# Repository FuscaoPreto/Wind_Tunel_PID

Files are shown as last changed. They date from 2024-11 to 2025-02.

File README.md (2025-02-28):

# Wind Tunnel Speed Control using PID

This project involves controlling the speed of a wind tunnel fan using a PID controller. The system uses environmental data from multiple sensors to compute airspeed and adjusts the fan speed accordingly.

The PID gains were discoveres by applying the Ziegler-Nichols method as a ruler.

## Sensors and Measurements

The project utilizes the following sensors:
- **HDC1080**: Measures temperature and humidity.
- **BME280**: Measures barometric pressure.
- **MPXV7002DP**: Measures differential air pressure.

## Airspeed and Air Density Calculation

The airspeed is derived using the Pitot tube formula, which relates the air pressure difference to velocity. The air density is computed using environmental measurements:

1. **Temperature in Kelvin**:
   $$T_k = T_{\text{Celsius}} + 273.15$$

2. **Saturation vapor pressure**:
   $$P_{\text{sat}} = 0.61078 \cdot \exp\left(\frac{17.27 \cdot T_{\text{Celsius}}}{T_{\text{Celsius}} + 237.3}\right)$$

3. **Water vapor pressure**:
   $$P_v = P_{\text{sat}} \cdot \frac{\text{Humidity}}{100.0}$$

4. **Dry air pressure**:
   $$P_d = P_{\text{atmospheric}} - P_v$$

5. **Air density**:
   $$\rho = \frac{P_d}{287.058 \cdot T_k} + \frac{P_v}{461.495 \cdot T_k}$$

6. **Airspeed**:
   $$v = \sqrt{\frac{2 \cdot P_{\text{differential}}}{\rho}}$$

## PID Control

The system employs a PID controller to maintain the target airspeed by adjusting the fan's speed.

### PID Formula
$$\text{PID output} = K_p \cdot e + K_i \int e \, dt + K_d \frac{de}{dt}$$

- **Proportional (P)**: $`e = v_{\text{target}} - v_{\text{measured'}}`$
- **Integral (I)**: Accumulated error over time.
- **Derivative (D)**: Rate of change of error.
#### Note:
The error in the code itself is multiplied by a air speed to RPM constant which is unique to my project, this is needed to calculate the correct PWM duty cycle.

## Code Logic

### Initialization
- Configure sensors (HDC1080 and BME280) using I²C.
- Initialize moving average arrays for pressure and RPM readings.
- Set up PWM for fan speed control.
- Attach an interrupt for tachometer readings.

### Main Functions
#### `updateData()`
Reads data from sensors and calculates:
- Air density ($`\rho`$)
- Airspeed ($`v`$)

#### `tacometroInterrupt()`
Triggered on tachometer pulses:
- Calculates RPM.
- Updates moving averages for RPM and pressure.
- Computes airspeed and PID output.
- Adjusts fan speed via PWM.

#### `loop()`
Continuously prints real-time data for debugging.

### Hardware Configuration
- **Analog Pin (1)**: Reads differential pressure sensor.
- **Tachometer Pin (15)**: Measures fan RPM.
- **PWM Pin (16)**: Controls fan speed.
- **SDA Pin (12), SCL Pin (11)**: I²C communication with HDC1080 and BME280.

## Libraries Used
- [ClosedCube_HDC1080](https://github.com/closedcube/ClosedCube_HDC1080)
- [BME280](https://github.com/finitespace/BME280)

## Setup and Usage
1. Connect the sensors and configure pins as per the hardware setup.
2. Upload the code to an Arduino or ESP32 board.
3. Adjust PID constants (`K_p`, `K_i`, `K_d`) for your wind tunnel.
4. Monitor serial output for real-time airspeed and PID performance.

## Images

Here are photos of the wind tunnel setup and key components:
   Body:
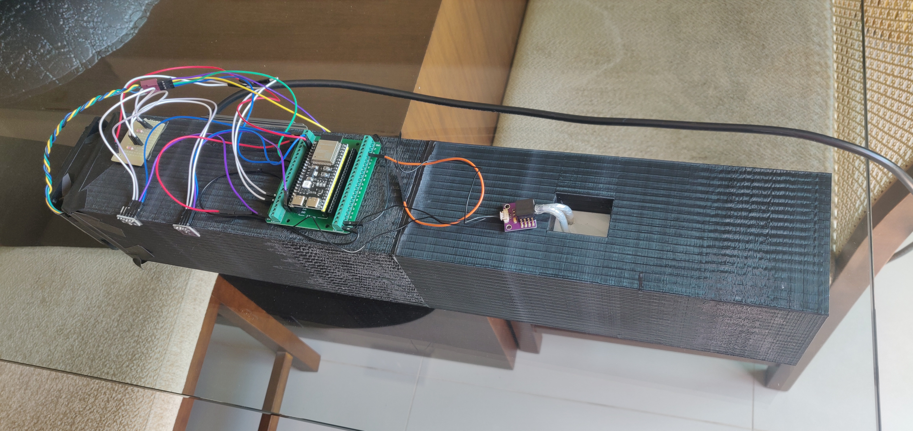
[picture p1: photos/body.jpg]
body
      
   Body (Alternate View):
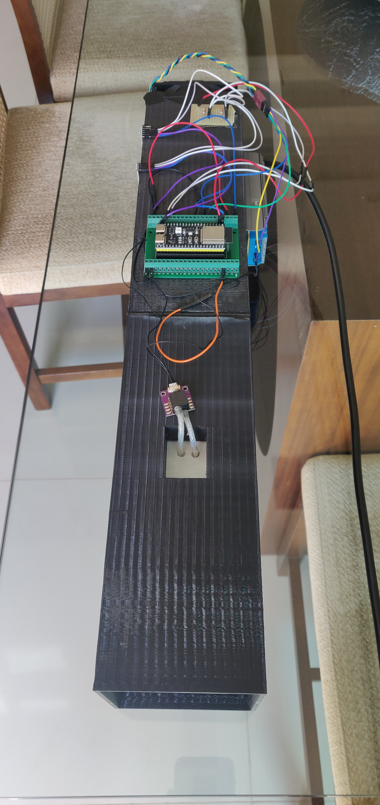
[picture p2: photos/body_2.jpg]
body vertical
      
   Mouth (Pitot Tube View):
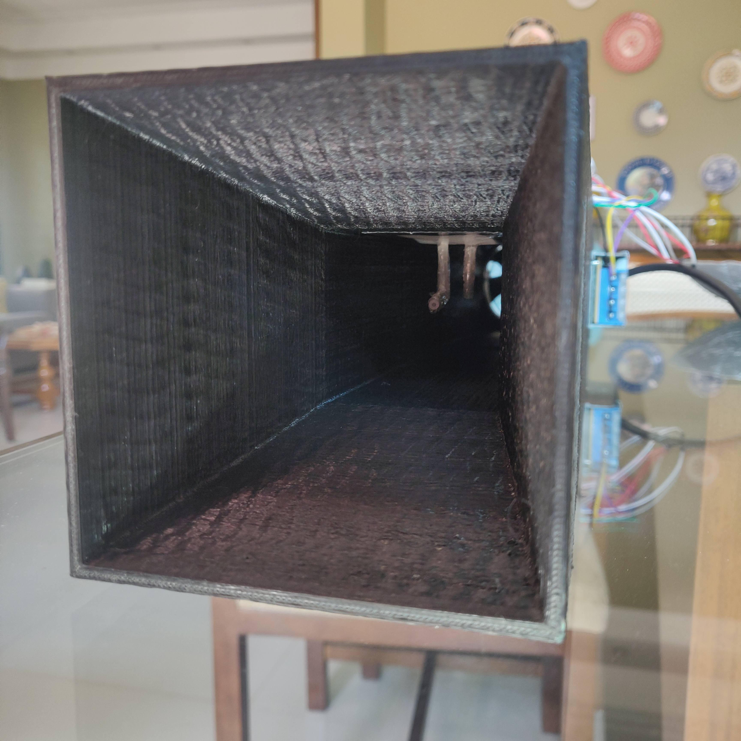
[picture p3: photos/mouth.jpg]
mouth


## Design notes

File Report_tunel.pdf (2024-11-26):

# Report tunel

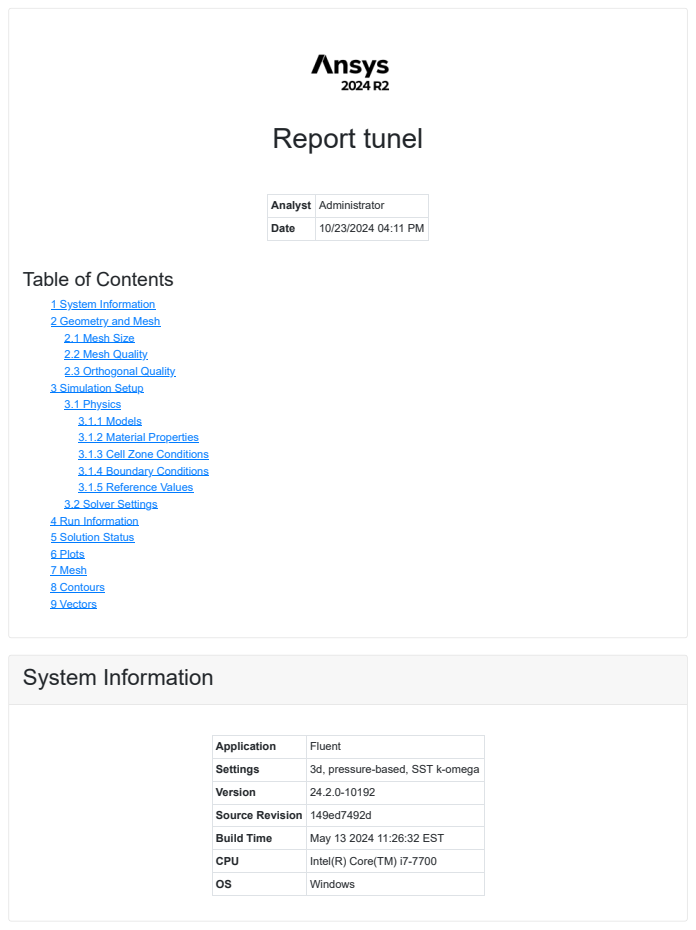
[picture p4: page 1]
System Information

Analyst | Administrator
Date | 10/23/2024 04:11 PM

Table of Contents

1 System Information
2 Geometry and Mesh
2.1 Mesh Size
2.2 Mesh Quality
2.3 Orthogonal Quality
3 Simulation Setup
3.1 Physics
3.1.1 Models
3.1.2 Material Properties
3.1.3 Cell Zone Conditions
3.1.4 Boundary Conditions
3.1.5 Reference Values
3.2 Solver Settings
4 Run Information
5 Solution Status
6 Plots
7 Mesh
8 Contours
9 Vectors

Application | Fluent
Settings | 3d, pressure-based, SST k-omega
Version | 24.2.0-10192
Source Revision | 149ed7492d
Build Time | May 13 2024 11:26:32 EST
CPU | Intel(R) Core(TM) i7-7700
OS | Windows

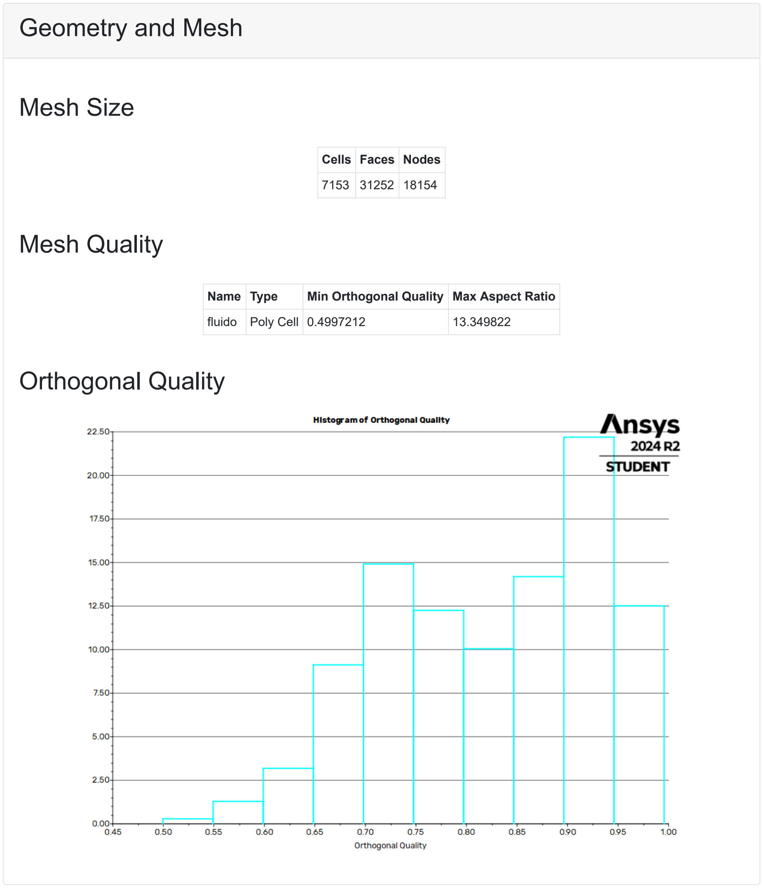
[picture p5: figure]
Geometry and Mesh; Mesh Size; Mesh Quality; Orthogonal Quality; Cells; Faces; Nodes; Name; Type; Min Orthogonal Quality; Max Aspect Ratio; fluido; Poly Cell

# Simulation Setup

# Physics

# Models

# Material Properties

# Cell Zone Conditions

# Boundary Conditions

Model | Settings
Space | 3D
Time | Steady
Viscous | SST k-omega turbulence model

Fluid

- air
Density | 1.225 kg/m^3
Cp (Specific Heat) | 1006.43 J/(kg K)
Thermal Conductivity | 0.0242 W/(m K)
Viscosity | 1.7894e-05 kg/(m s)
Molecular Weight | 28.966 kg/kmol
- Solid

aluminum

Density | 2719 kg/m^3
Cp (Specific Heat) | 871 J/(kg K)
Thermal Conductivity | 202.4 W/(m K)
- Fluid

fluido

Material Name | air
Specify source terms? | no
Frame Motion? | no
Laminar zone? | no
Porous zone? | no
- Inlet
- failed-inlet-fluido
Reference Frame | Absolute
Gauge Total Pressure [Pa] | 0
Supersonic/Initial Gauge Pressure [Pa] | 0
Direction Specification Method | Normal to Boundary

# Solver Settings

# Reference Values

Build artificial walls to prevent reverse flow? | no
Turbulence Specification Method | Intensity and Viscosity Ratio
Turbulent Intensity [%] | 5
Turbulent Viscosity Ratio | 10
- Outlet

failed-outlet-fluido

Reference Frame | Relative to Adjacent Cell Zone
Mass Flow Specification Method | Mass Flow Rate
Mass Flow Rate [kg/s] | 0.1041667
Supersonic/Initial Gauge Pressure [Pa] | 0
Turbulence Specification Method | Intensity and Viscosity Ratio
Turbulent Intensity [%] | 5
Turbulent Viscosity Ratio | 10

Wall

- failed
Wall Motion | Stationary Wall
Shear Boundary Condition | No Slip
Wall Surface Roughness | Standard
Wall Roughness Height [m] | 0
Wall Roughness Constant | 0.5
Area | 1 m^2
Density | 1.225 kg/m^3
Enthalpy | 0 J/kg
Length | 1 m
Pressure | 0 Pa
Temperature | 288.16 K
Velocity | 1 m/s
Viscosity | 1.7894e-05 kg/(m s)
Ratio of Specific Heats | 1.4
Yplus for Heat Tran. Coef. | 300
Reference Zone | failed-outlet-fluido
- Equations
Flow | True
Turbulence | True
- Numerics
Absolute Velocity Formulation | True

Pseudo Time Explicit Relaxation Factors

Density | 1

Body Forces | 1
Turbulent Kinetic Energy | 0.75
Specific Dissipation Rate | 0.75
Turbulent Viscosity | 1
Explicit Momentum | 0.5
Explicit Pressure | 0.5
- Pressure-Velocity Coupling
Type | Coupled
Pseudo Time Method (Global Time Step) | True

Discretization Scheme

Pressure | Second Order
Momentum | Second Order Upwind
Turbulent Kinetic Energy | Second Order Upwind
Specific Dissipation Rate | Second Order Upwind
- Solution Limits
Minimum Absolute Pressure [Pa] | 1
Maximum Absolute Pressure [Pa] | 5e+10
Minimum Static Temperature [K] | 1
Maximum Static Temperature [K] | 5000
Minimum Turb. Kinetic Energy [m^2/s^2] | 1e-14
Minimum Spec. Dissipation Rate [s^-1] | 1e-20
Maximum Turb. Viscosity Ratio | 100000

# Run Information

Number of Machines | 1
Number of Cores | 1
Case Read | 2.746 seconds
Iteration | 243.856 seconds
AMG | 165.586 seconds
Virtual Current Memory | 0.49369 GB
Virtual Peak Memory | 1.49084 GB
Memory Per M Cell | 19.8388

# Solution Status

## Iterations: 1000

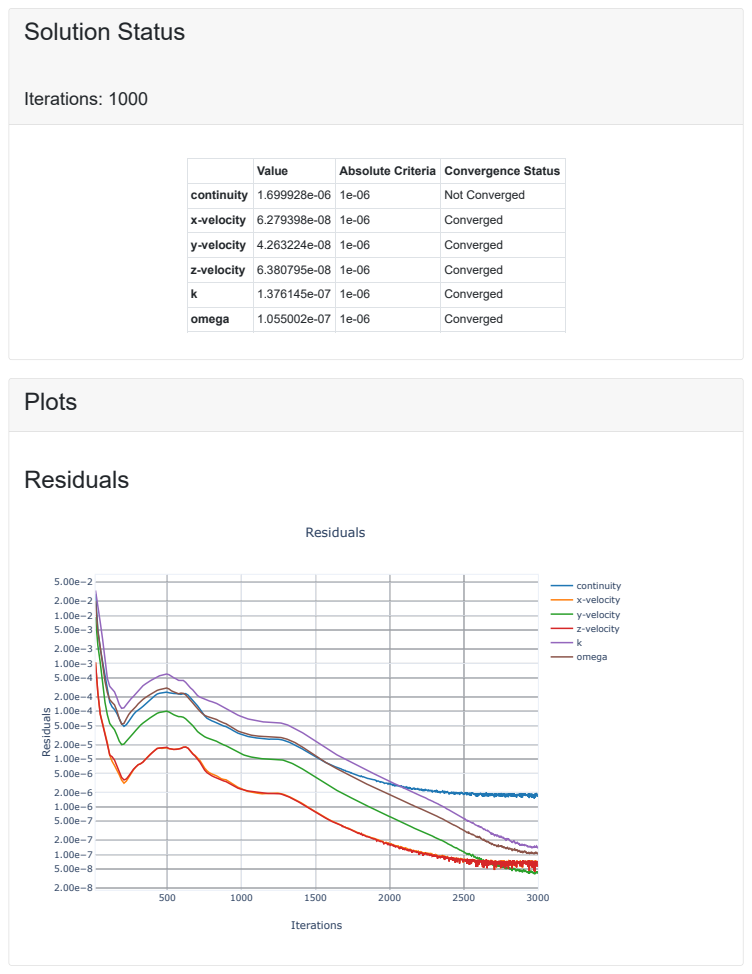
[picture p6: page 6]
Plots; Residuals; continuity; x-velocity y-velocity z-velocity k omega; Iterations

Value | Absolute Criteria | Convergence Status

continuity | 1.699928e-06 | 1e-06 | Not Converged
x-velocity | 6.279398e-08 | 1e-06 | Converged
y-velocity | 4.263224e-08 | 1e-06 | Converged
z-velocity | 6.380795e-08 | 1e-06 | Converged
k | 1.376145e-07 | 1e-06 | Converged
omega | 1.055002e-07 | 1e-06 | Converged

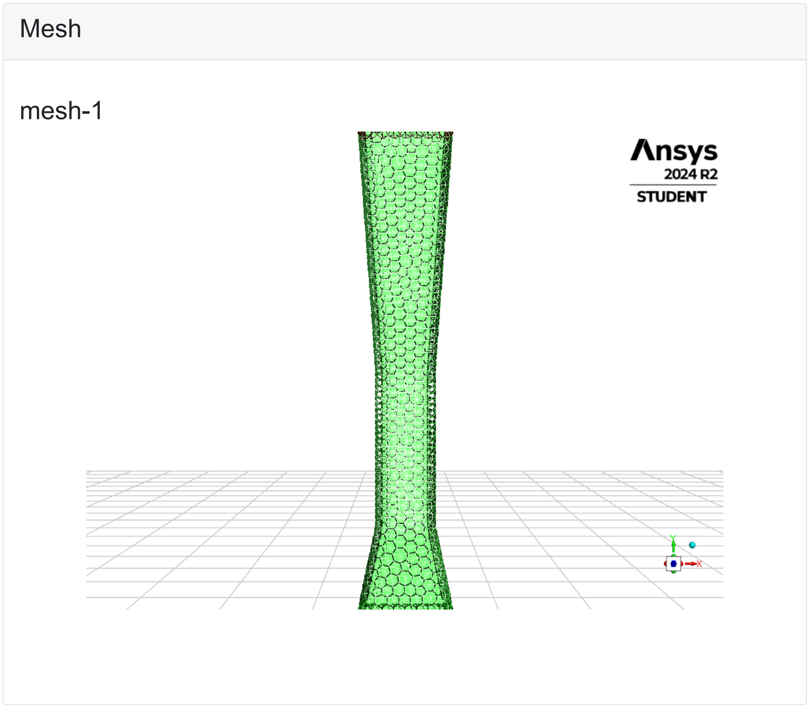
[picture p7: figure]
Mesh; mesh-1

# Contours

# turbulencia

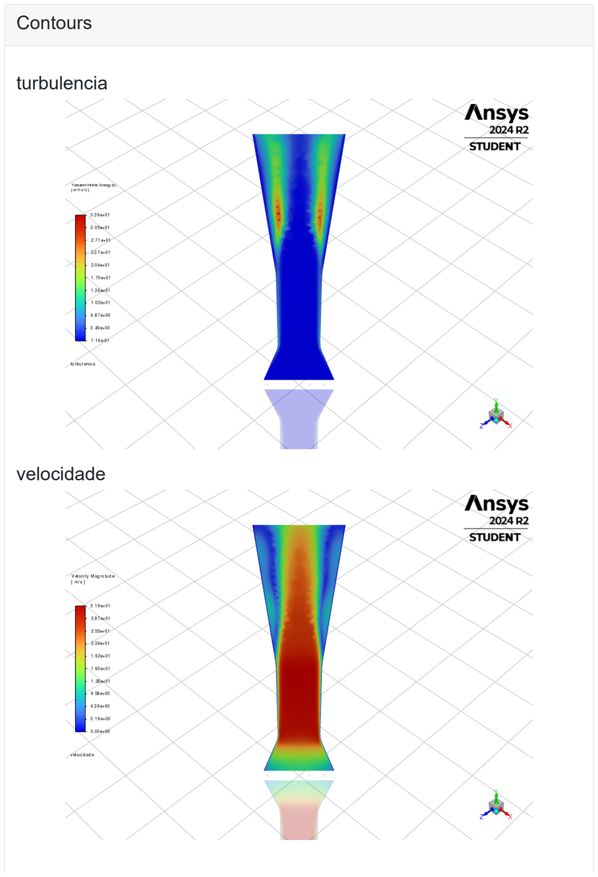
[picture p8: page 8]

# velocidade

# pressao

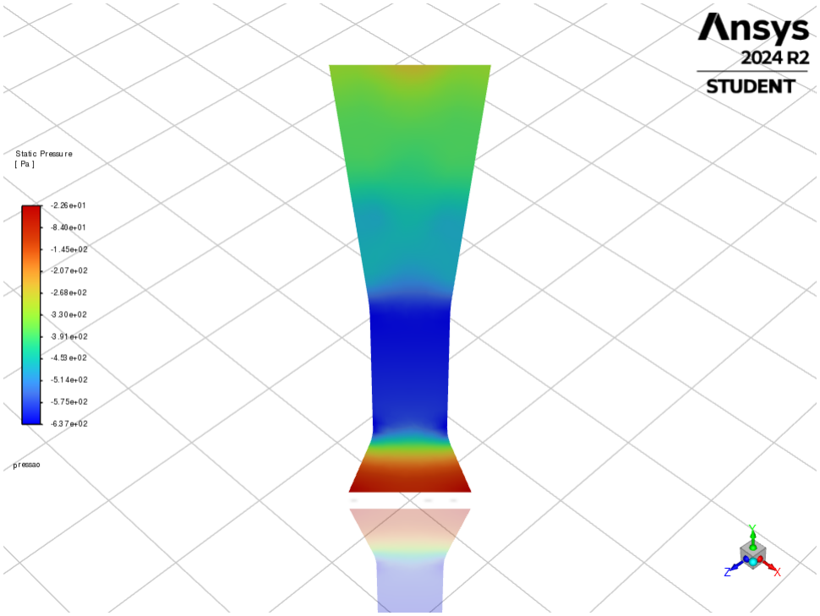
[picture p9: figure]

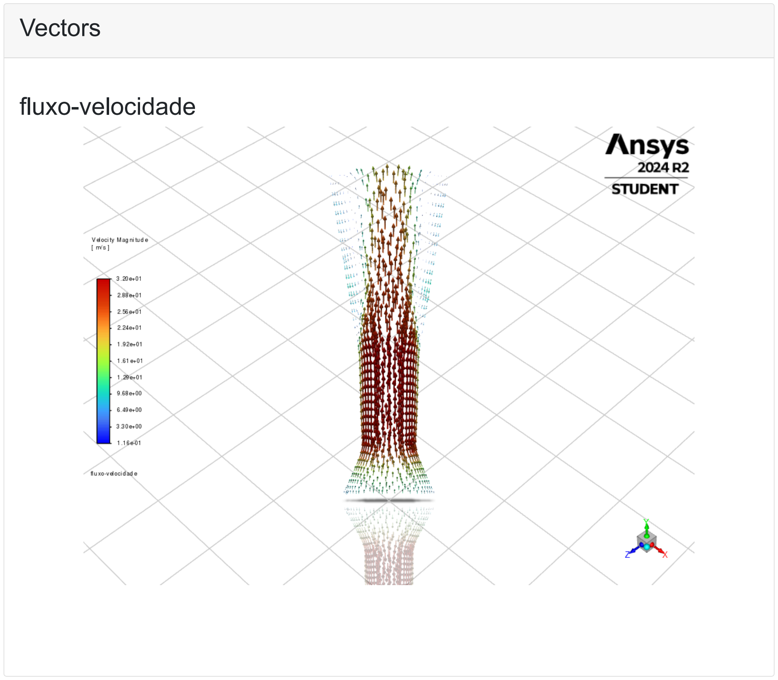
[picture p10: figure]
Vectors; fluxo-velocidade

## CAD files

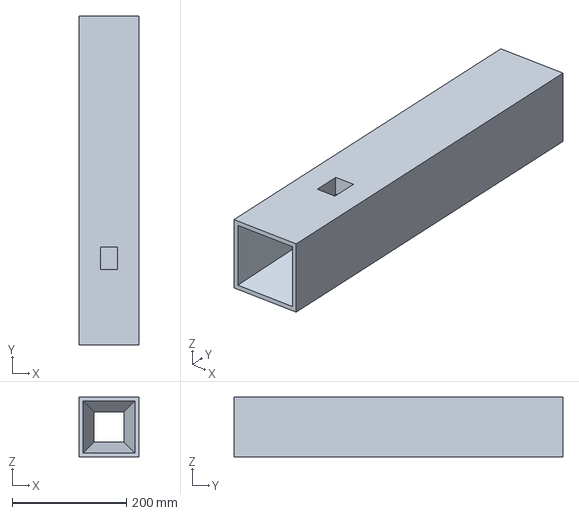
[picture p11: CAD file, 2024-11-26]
Tunel de vento.FCStd
105.0 x 577.0 x 105.0 mm

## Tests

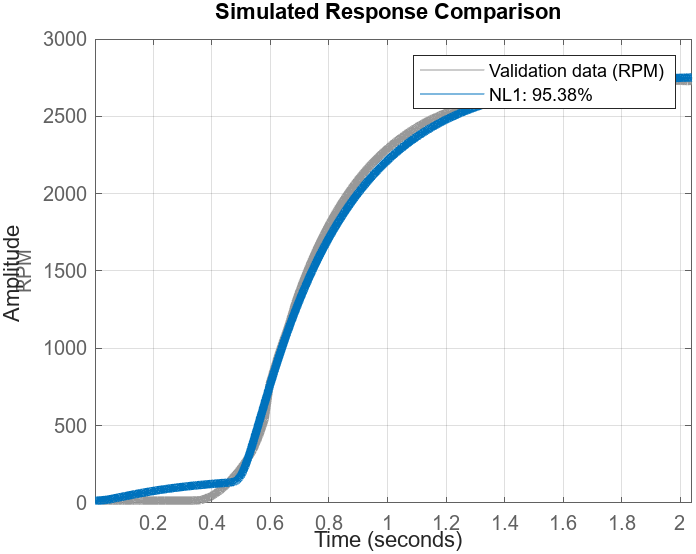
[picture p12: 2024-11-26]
MATLAB/Images and results/GestvsReal.png

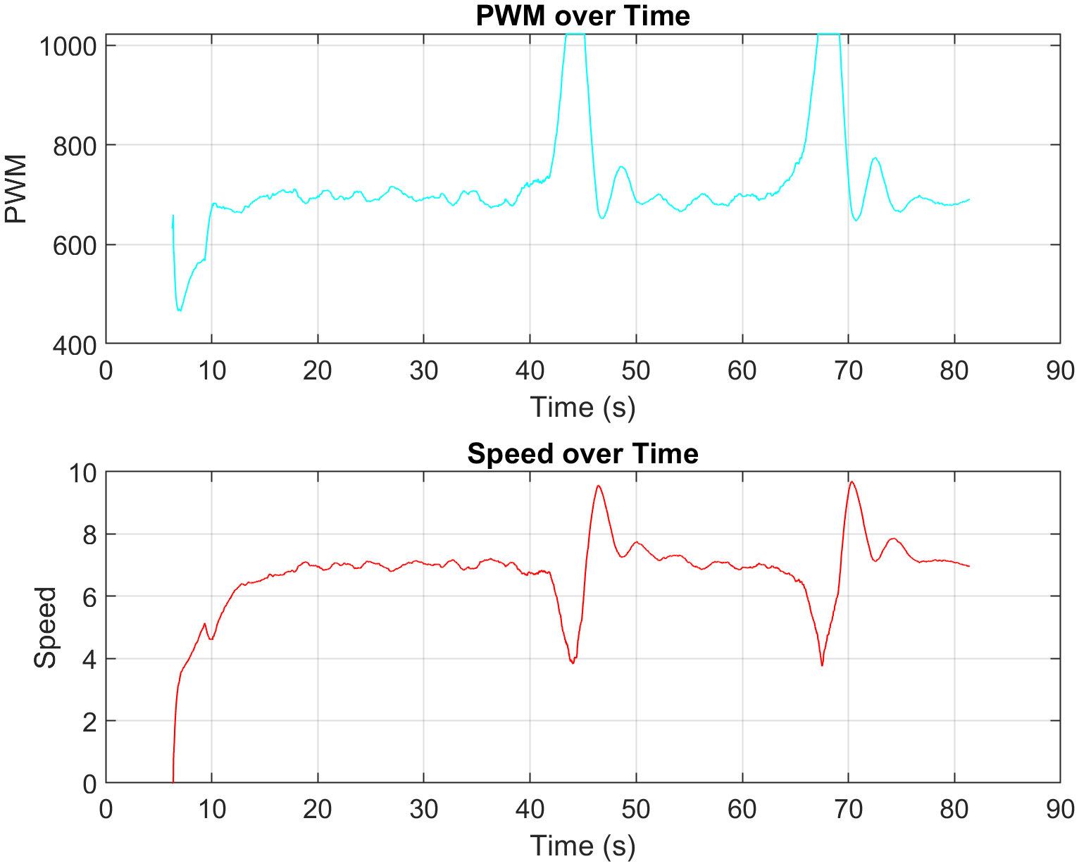
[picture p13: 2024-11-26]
MATLAB/Images and results/pwm_speed_over_time.png

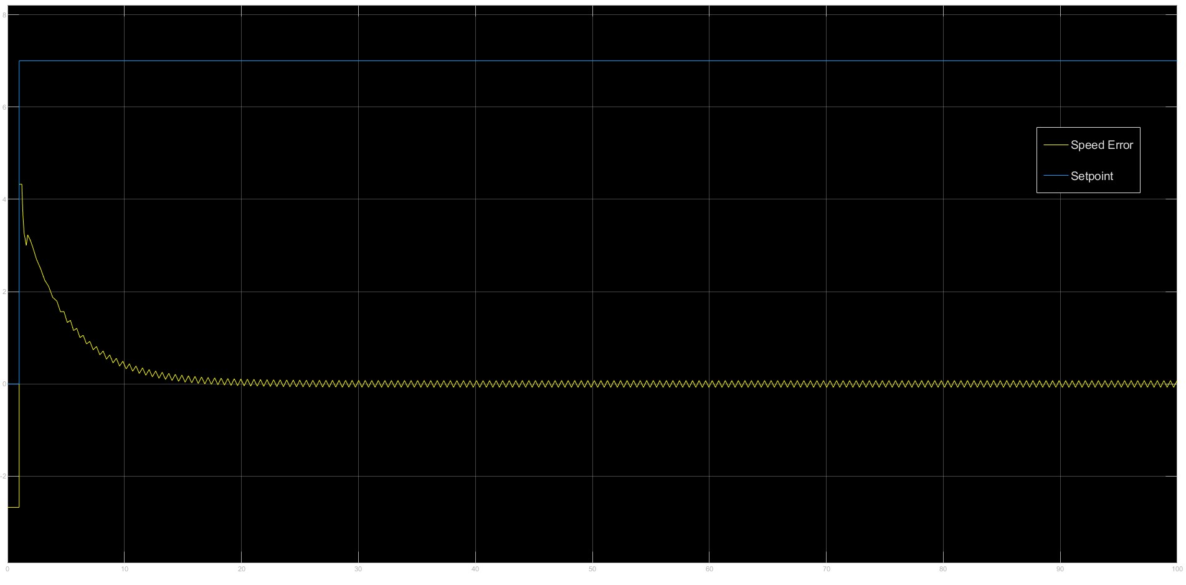
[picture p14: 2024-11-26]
MATLAB/Images and results/scope_vel.jpg

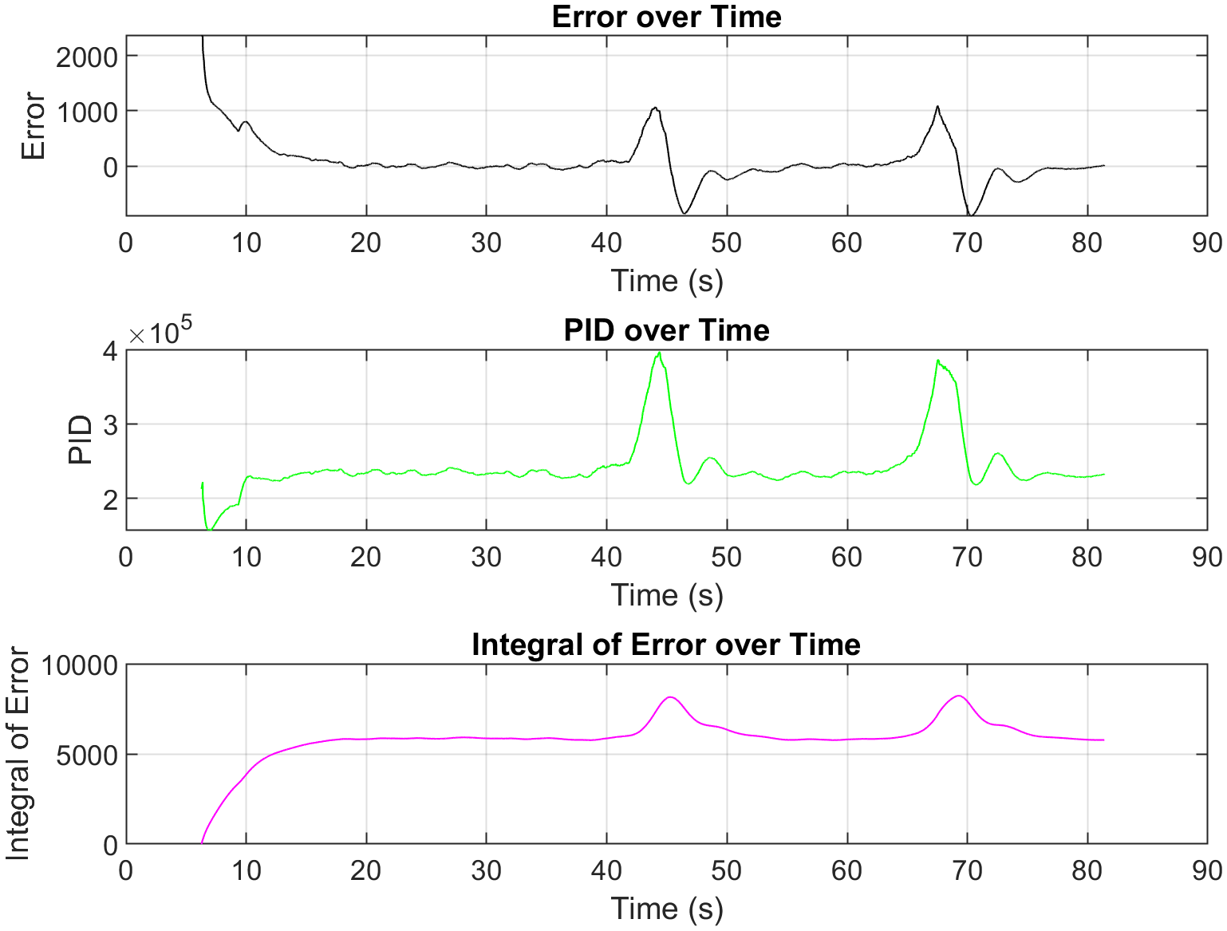
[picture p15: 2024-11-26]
MATLAB/Images and results/error_pid_integral_over_time.png

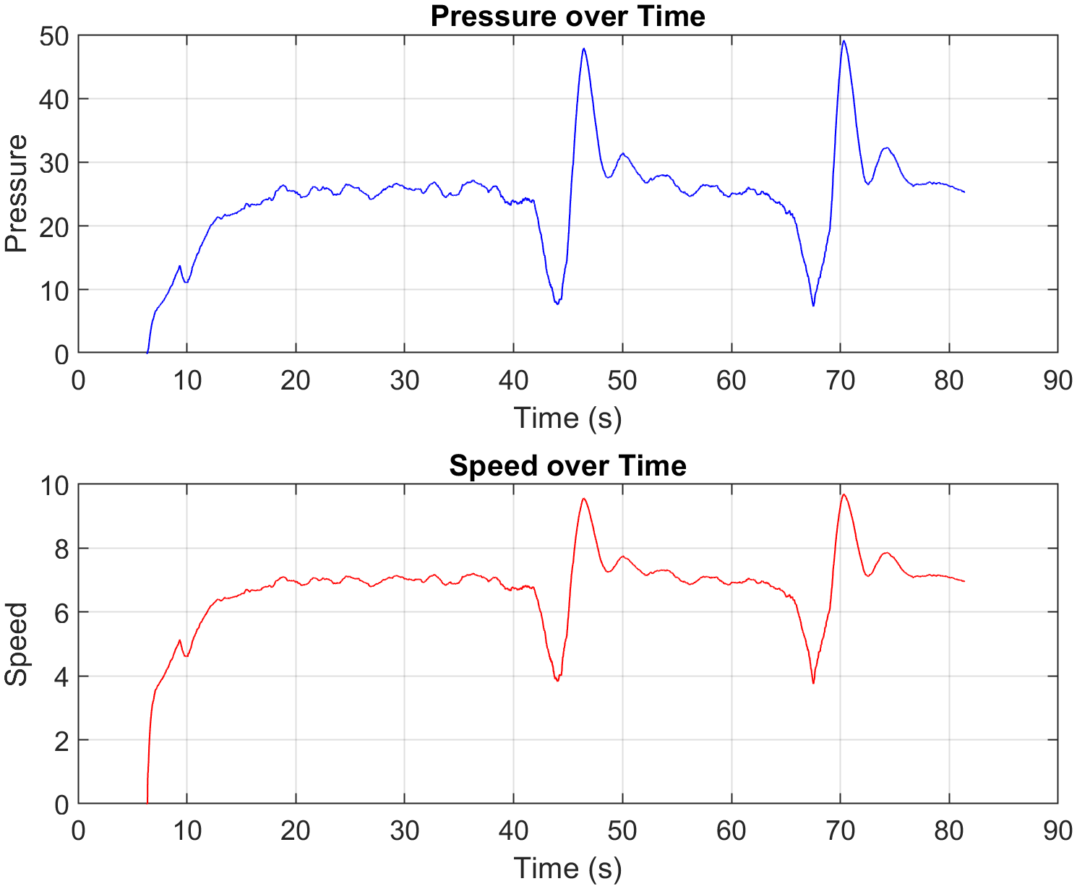
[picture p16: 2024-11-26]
MATLAB/Images and results/pressure_speed_over_time.png

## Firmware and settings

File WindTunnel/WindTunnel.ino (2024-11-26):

#include <Wire.h>
#include "ClosedCube_HDC1080.h"
#include <Bme280.h>

// Definições de pinos e constantes
const int analogPin = 1;      // Pino ADC
const int windowAnalog = 100;  // Tamanho da janela da média móvel
const int windowRPM = 50;     // Tamanho da janela para o cálculo da média móvel de RPM
const int tacometroPin = 15;  // Pino onde o sinal do tacômetro está conectado
const int pwmPin = 16;        // Pino de saída PWM
const int pwmRes = 10;        // Resolução do PWM
const int pwmFreq = 25000;    // Frequência do PWM
const int pinSDA = 12;
const int pinSCL = 11;
// Variáveis para os arrays de média móvel e índices
volatile int analogValues[windowAnalog];  // Array para armazenar os valores da janela de leituras analógicas
volatile int analogIndex = 0;             // Índice atual para a média móvel de leituras analógicas
volatile float analogSum = 0;             // Soma das leituras analógicas para média móvel
volatile int rpmValues[windowRPM];        // Array para armazenar os valores da janela de RPM
volatile int rpmIndex = 0;                // Índice atual para a média móvel de RPM
volatile float rpmSum = 0;                // Soma das leituras de RPM para média móvel

// Variáveis para controle de tempo e cálculo de RPM
volatile unsigned long lastPulseTime = 0;  // Tempo do último pulso do tacômetro
volatile unsigned long pulseInterval = 0;  // Intervalo entre os pulsos do tacômetro
volatile int rpm = 0;                      // Velocidade do motor em RPM
volatile float filteredRPM = 0;

// Variáveis para cálculo de velocidade do ar e pressão
volatile float airspeed = 0;
volatile double pressure = 0;
volatile double volts = 0;
volatile int offset = 0;
volatile double atmPressao = 0;
volatile double umidade = 0;
volatile double temperatura = 0;
volatile double tempk = 0;
volatile double psat = 0;
volatile double pv = 0;
volatile double pd = 0;
volatile double pha = 0;
volatile float filteredAnalog = 0;
// Variáveis para controle PID
double integral = 0, output = 0, dt = 0;
double ki = 27.6;
double kp = 138;
double kd = 43.125;
volatile double proportional = 0, previous = 0, derivative = 0, error = 0;
double targetSpeed = 8.0;
volatile double pid = 0;


// Variáveis de PWM e tempo
int pwmValue = 0;                     // Valor inicial do PWM
unsigned long lastPwmUpdateTime = 0;  // Para controlar o tempo de incremento ou decremento do PWM

//Objects
ClosedCube_HDC1080 hdc;
Bme280TwoWire bme;


void updateData() {
  temperatura = hdc.readTemperature();
  umidade = hdc.readHumidity();
  atmPressao = bme.getPressure();
  tempk = temperatura + 273.15;
  psat = 0.61078 * exp((17.27 * temperatura) / (temperatura + 237.3));
  pv = psat * (umidade / 100.0);
  pd = atmPressao - pv;
  pha = (pd / (287.058 * tempk)) + (pv / (461.495 * temperatura + 273.15));
}

void IRAM_ATTR tacometroInterrupt() {
  unsigned long currentTime = micros();


  // Calcula o intervalo entre pulsos
  if (lastPulseTime > 0) {
    pulseInterval = currentTime - lastPulseTime;       // Intervalo entre os pulsos
    rpm = 60000000.0 / (pulseInterval * 2);            // Calcula a RPM com base no intervalo
    int analogValue = analogRead(analogPin) - offset;  // Lê o valor analógico e ajusta o offset

    // Calcula a média dos valores na janela
    float meanAnalog = analogSum / windowAnalog;
    float thresholdAnalog = meanAnalog * 0.02;  // Define o limite como 1% da média atual

    // Verifica se o valor lido está dentro do limite de 10% em relação à média
    if (abs(analogValue - meanAnalog) <= thresholdAnalog) {
      // Remove o valor mais antigo da soma e atualiza o array
      analogSum -= analogValues[analogIndex];
      analogValues[analogIndex] = analogValue;
      analogSum += analogValue;

      // Atualiza o índice da janela circular
      analogIndex = (analogIndex + 1) % windowAnalog;
    }

    // Calcula a média móvel sem incluir outliers
    filteredAnalog = analogSum / windowAnalog;

    // Calcula a média dos valores na janela
    float meanRPM = rpmSum / windowRPM;
    float thresholdRPM = meanRPM * 0.2;  // Define o limite como 1% da média atual

    // Verifica se o valor lido está dentro do limite de 10% em relação à média
    if (abs(rpm - meanRPM) <= thresholdRPM) {
      // Remove o valor mais antigo da soma e atualiza o array
      rpmSum -= rpmValues[rpmIndex];
      rpmValues[rpmIndex] = rpm;
      rpmSum += rpm;

      // Atualiza o índice da janela circular
      rpmIndex = (rpmIndex + 1) % windowRPM;
    }

    // Calcula a média móvel sem incluir outliers
    filteredRPM = rpmSum / windowRPM;

    // Conversão para tensão, pressão e velocidade do ar
    volts = filteredAnalog * 3.3 / 4096;
    pressure = volts * (4000 / 3.3) - 2000;
    if (pressure < 0) pressure = 0.0001;
    airspeed = sqrt(2 * (pressure / pha));

    //if(integral>0) pressure=0.0001;
    error = targetSpeed - airspeed;
    error = error * (1750.0 / 5.2);
    proportional = error;
    dt = pulseInterval / 1000000.0;
    integral += error * dt;
    derivative = (error - previous) / dt;
    previous = error;
    pid = (kp * proportional) + (ki * integral) + (kd * derivative);
    pwmValue = pid / (1750.0 / 5.2);

    if (pwmValue < 256) {
      pwmValue = 256;
    }
    if (pwmValue > 1023) {
      pwmValue = 1023;
    }


    ledcWrite(pwmPin, pwmValue);
  }

  // Atualiza o tempo do último pulso
  lastPulseTime = currentTime;
}

void setup() {
  offset = analogRead(analogPin) - 2048;
  Serial.begin(921600);  // Inicializa a comunicação serial
  for (int i = 0; i < windowAnalog; i++) {
    analogValues[i] = 2048;  // Inicializa o array com 2048, valor base para nenhuma pressão
    analogSum += analogValues[i];
  }
  for (int i = 0; i < windowRPM; i++) {
    rpmValues[i] = 3400;  // Inicializa o array com 2048, valor base para nenhuma pressão
    rpmSum += rpmValues[i];
  }
  pinMode(tacometroPin, INPUT_PULLUP);  // Configura o pino com pull-up interno
  Wire.begin(pinSDA, pinSCL);
  hdc.begin(0x40);
  bme.begin(Bme280TwoWireAddress::Primary);

  Serial.println("Filtros iniciados");
  delay(1000);
  Serial.println("5 Segundos para iniciar");
  delay(1000);
  Serial.println("4 Segundos para iniciar");
  delay(1000);
  Serial.println("3 Segundos para iniciar");
  delay(1000);
  Serial.println("2 Segundos para iniciar");
  delay(1000);
  Serial.println("1 Segundos para iniciar");
  delay(1000);

  updateData();

  attachInterrupt(digitalPinToInterrupt(tacometroPin), tacometroInterrupt, FALLING);

  // Configuração do PWM utilizando a função ledcAttach
  ledcAttach(pwmPin, pwmFreq, pwmRes);  // Associa o pino e configura a frequência e a resolução do PWM
}

void loop() {
  Serial.print(pwmValue);
  Serial.print(", ");
  Serial.print(pid);
  Serial.print(", ");
  Serial.print(error);
  Serial.print(", ");
  Serial.print(integral);
  Serial.print(", ");
  Serial.print(derivative);
  Serial.print(", ");
  Serial.print(filteredRPM);
  Serial.print(", ");
  Serial.print(pressure);
  Serial.print(", ");
  Serial.println(airspeed);
}
